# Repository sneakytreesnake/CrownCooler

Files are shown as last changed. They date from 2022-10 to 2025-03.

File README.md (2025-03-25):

# CrownCooler - Ring shaped CPAP cooling duct for Voron 3D printers
This mod is designed to adapt a fan mounted somewhere on the frame, through a CPAP tube and onto a "crown" shaped cooling duct. It has been designed for the Voron 2.4 and Voron Trident series of printers, mounting directly to the stealthburner X carriage.

 

This mod was developed to:
- be compatible with standard voron stealthburner carriage
- be compatible with all extruder combinations that are compatible with the stealthburner system, (CW1, CW2, Orbiter, LGX Lite, etc.)
- mount a Rapido HF/UHF hot end & Dragon SF/HF/UHF hot end 
- improve overall cooling performance by accomodating very large fans and intaking cool air from outside the heated enclosure
- provide uniform cooling from all directions
- be lightweight and easy to maintain
- work with klickyprobe & euclid probe.

The design of the crown duct creates a fluid vortex at the tip of the nozzle, resulting in high cooling performance. It was designed using commercial CFD software, and validated experimentally. There is a secondary air cooling route fed by the part cooling fan to prevent warping of the duct from hot end heat. 

**This mod is still a BETA. Expect issues - but let me know about them so I can fix them.**

## Dev Update (Mar 2025)
I've uploaded the Fusion 360 native CAD assembly.



I am currently testing the Dragon SF/HF version. Working well so far. 
My Rapido hotend is damaged so I can no longer test that one personally.

## Dev Update (Sept 2024)
I have added a trimmed down X carriage mount to fit the new duct. I've also added a adapter mount for the Euclid Probes. Let me know if there is interest for a Klicky mount and I will make one.

## Dev Update (August 2024)
I have created a Dragon (SF/HF) toolhead mount.  


Furthermore, I have created a new duct design. This combines the ideas I have created in the crown design, along with the tentacool duct. I'm still working on airflow optimisation but so far the performance is good.

The Dragon mount will be released in the coming days, and the duct will be released after some more testing.

## Dev Update (July 2024)
After a lot of experimenting with other cooling designs such as the [Tentacool](https://github.com/MirageC79/HextrudORT/tree/main/files/COOLING/TENTACOOL), I plan on merging the ideas produced from the V2.5 cooler, with the ideas from the Tentacool. I don't want to give a release date as it's a slow process, but a release is on the hoizon. 

Until then, I will build in support for other hot ends (dragon HF, Rapido HF, Rapido UHF for now. I am open to further requests). These will be release as soon as possible. The V2.5 duct and a modified Tentacool duct will be included in this release. I expect to release this by the end of July.

## V2.5 Update (February 2024)
The flow path has been updated in the latest version. It provides approximately **twice the cooling performance compared to the previous version!** In my testing, I was able to print 80degree angles at 30% fan rate (WS7040) with an enclosure temperature of 70C, 0.6mm nozzle size and 0.3mm layer height.

  

# Gallery

  

## CFD results:
You can clearly see a vortex being formed around the ring. This creates a cycle of air that rapidly carries heat from the printed part, allowing printong of steep overhangs.

 

# Part Cooling Fan Options

There are a number of part cooling fan options to choose from, depending on your intended use case.

### 4028 fan



A "medium" performance option is to use a 4028 fan on the end of the CPAP tube. This solution is best suited for ABS and similiar materials that do not require high amounts of part cooling. I do not recommend this option for printing PLA at high speeds.
A 4028 to CPAP tube adapter part is included in the STL files folder.

Recommended 4028 fans include:
- Sanyo 9GAX0412P3S001
- Delta FFB0412UHN-SM36

### 7040 blower fan



A "high" performance is to use a 7040 blower fan on the end of the CPAP tube. This solution is best suited for printing PLA & PETG & ABS at very high speeds.

A 7040 blower fan mount can be found [here.](https://www.printables.com/model/324265-ws7040-centrifugal-blower-fan-mount)

I recommend the WS7040 along with the controller board. I purchased mine from [Trianglelab here.](https://www.aliexpress.com/item/1005003822117604.html)

# BOM
- Coming soon...
  
# Installation instructions 
- This mod uses the standard stealthburner X carriage parts. T
- This mod should work with all types of extruder mounting parts, including CW2 (however, I have not yet tested it). I use the orbiter V2 extruder mount found [here](https://github.com/sneakytreesnake/StealthOrbiter).
- Print the cooling duct with no supports, file in STL folder. Use standard Voron print setting (0.6mm nozzle is acceptable)
- Only euclid and klicky probes are compatible at the moment. Use the offset klicky mount for HF hot ends, use the tall offset clock mount for UHF hot ends.

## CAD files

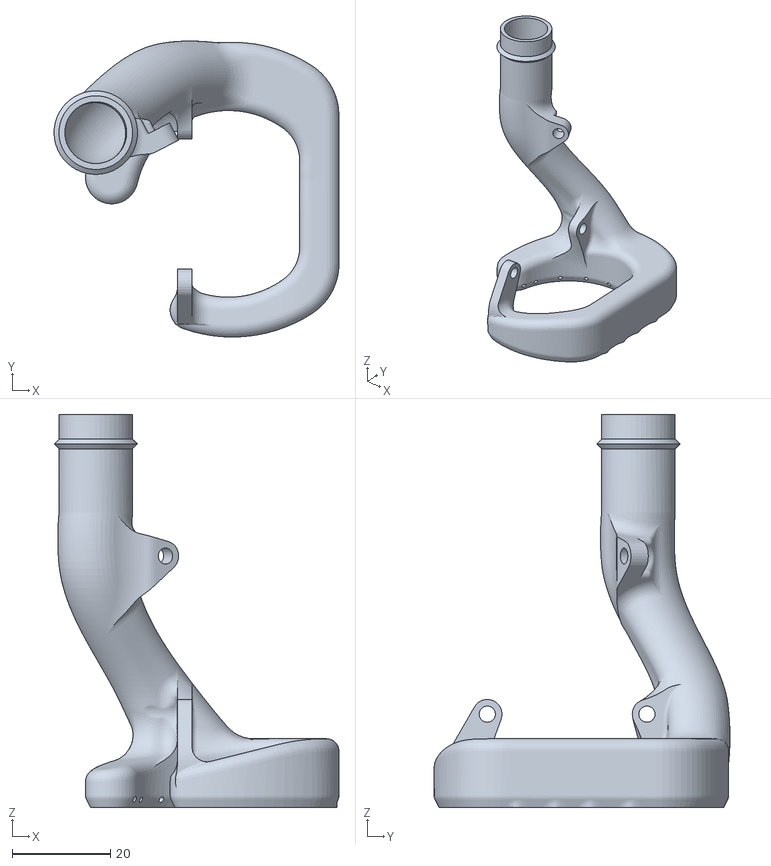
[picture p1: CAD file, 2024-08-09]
STL/Duct/MainDuct_BETA1.stl
58.0 x 60.3 x 80.0

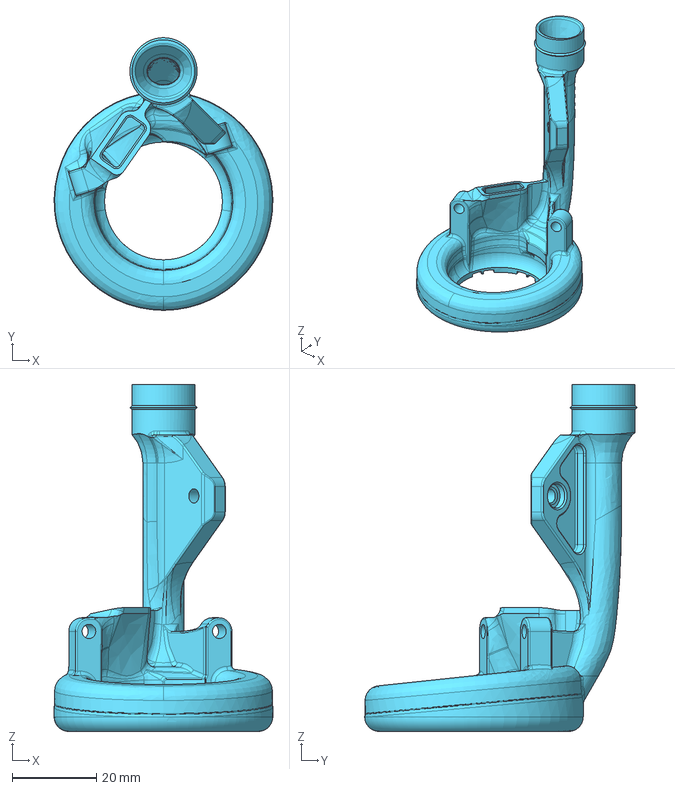
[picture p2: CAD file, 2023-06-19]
CAD/CrownCooler_Duct_RapidoUHF-15mmTube.step
52.0 x 64.8 x 82.5 mm

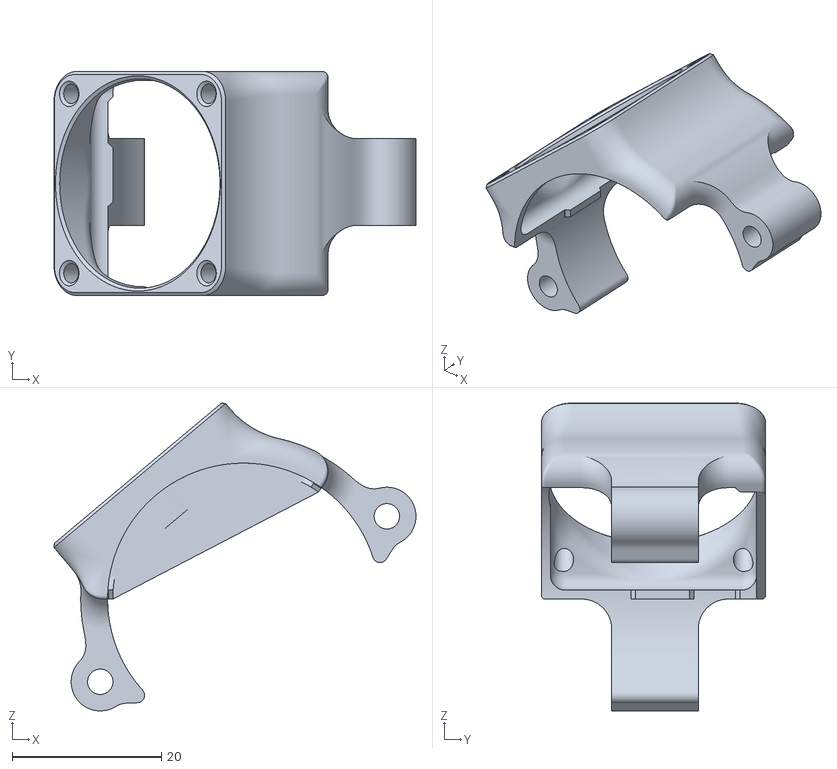
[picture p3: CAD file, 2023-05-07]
STL/ExtruderCooler/CrownCooler_ExtruderFanShroud.stl
48.5 x 30.0 x 41.2

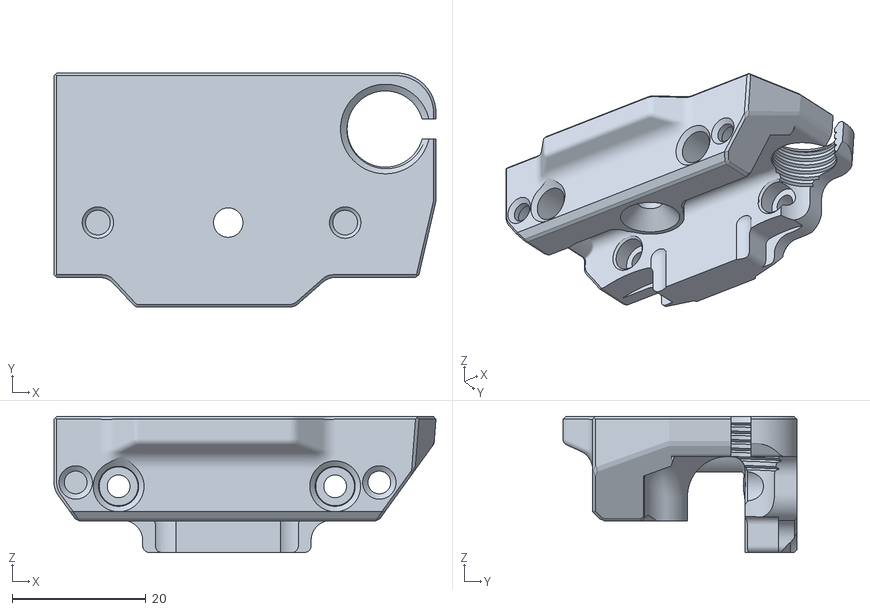
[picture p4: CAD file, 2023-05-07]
STL/ExtruderMount/CrownCooler_Orbitermount_Standard_PG7.stl
57.2 x 35.0 x 20.4

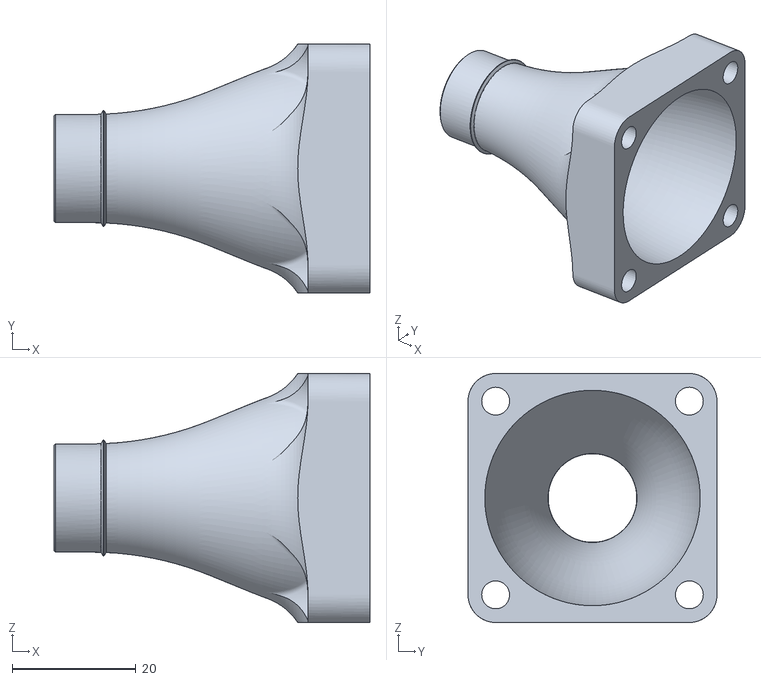
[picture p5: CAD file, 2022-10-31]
STL/FanMounts/4028 Fan/CrownCooler_4028FanCPAPAdapter.stl
51.0 x 40.2 x 40.2

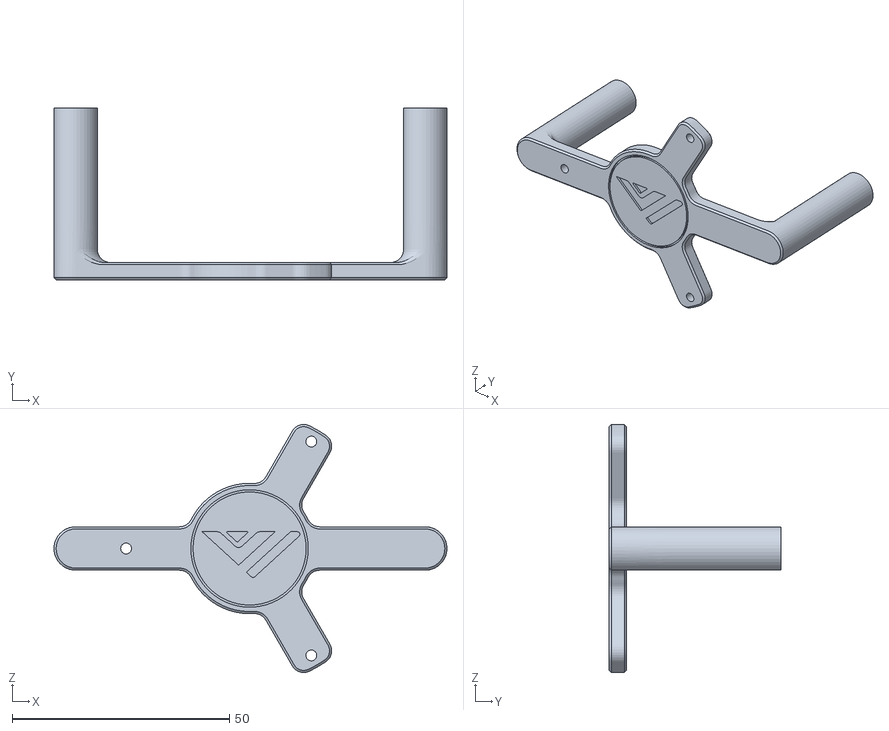
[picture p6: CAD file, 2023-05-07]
STL/FanMounts/WS7040 Fan/CPAPFanMount.stl
90.4 x 39.5 x 57.1

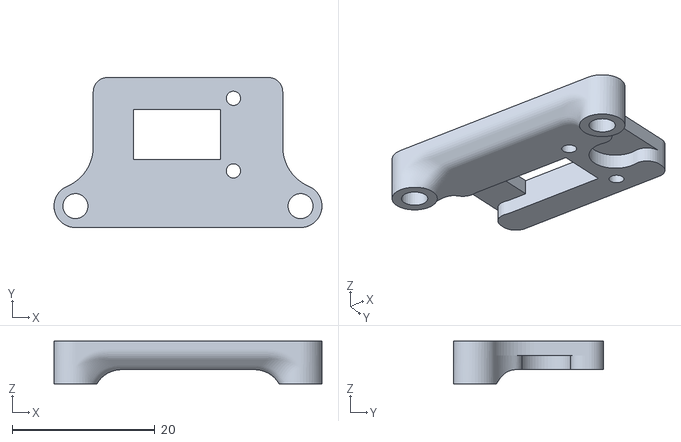
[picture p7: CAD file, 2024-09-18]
STL/ProbeMounts/EuclidProbeMountV2.stl
37.5 x 21.0 x 6.00

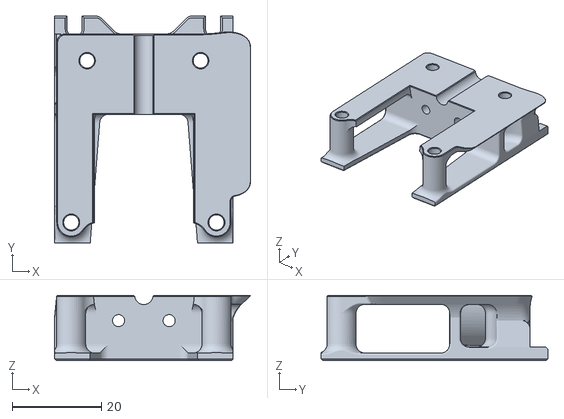
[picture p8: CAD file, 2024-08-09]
STL/Toolhead/CrownCooler_Toolhead_DragonHF_Rear.stl.stl
43.9 x 50.8 x 14.6

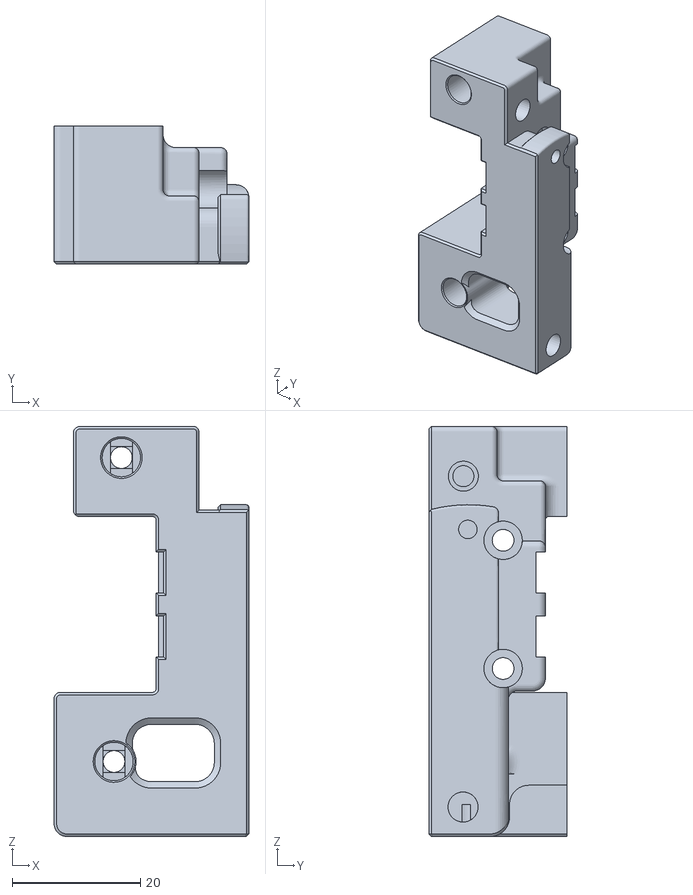
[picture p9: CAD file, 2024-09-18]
STL/Xcarriage/MGN12_X_Carriage_CW2_TRIMMED_left_V1.stl
30.4 x 21.6 x 64.0

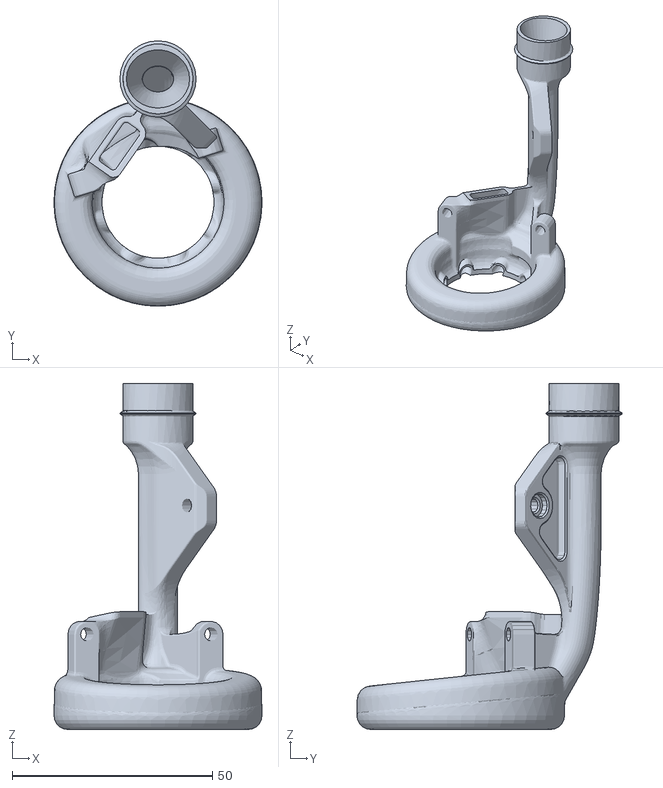
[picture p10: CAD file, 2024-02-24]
STL/Duct/CrownCooler_Duct_RapidoUHF_V2.5.stl
52.0 x 66.4 x 86.5

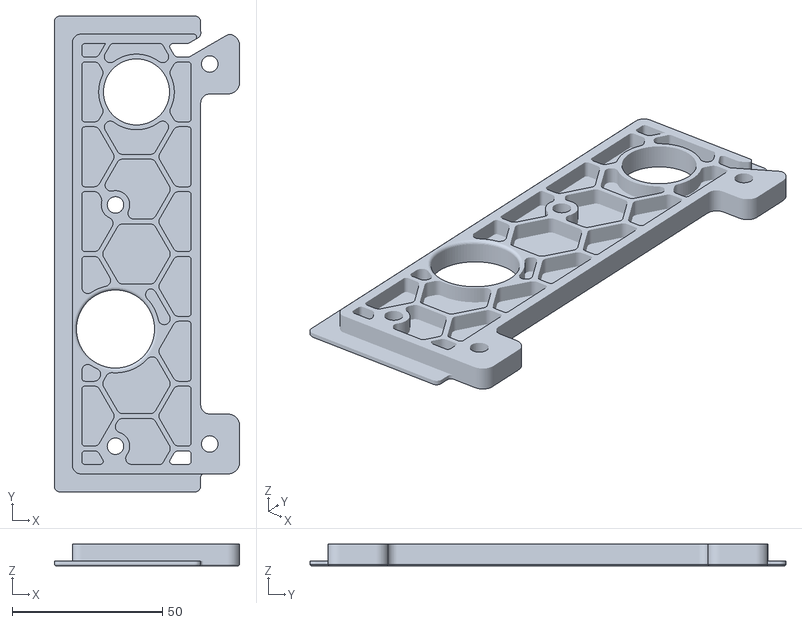
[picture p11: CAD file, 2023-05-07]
STL/FanMounts/WS7040 Fan/CrownCooler_ExhaustCover.stl
61.8 x 158.6 x 7.20

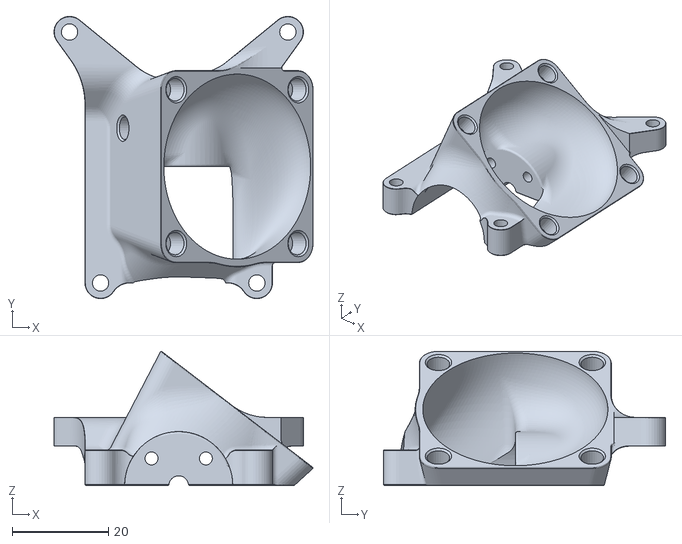
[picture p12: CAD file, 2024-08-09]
STL/Toolhead/CrownCooler_Toolhead_DragonHF_Front.stl.stl
53.9 x 58.7 x 27.9

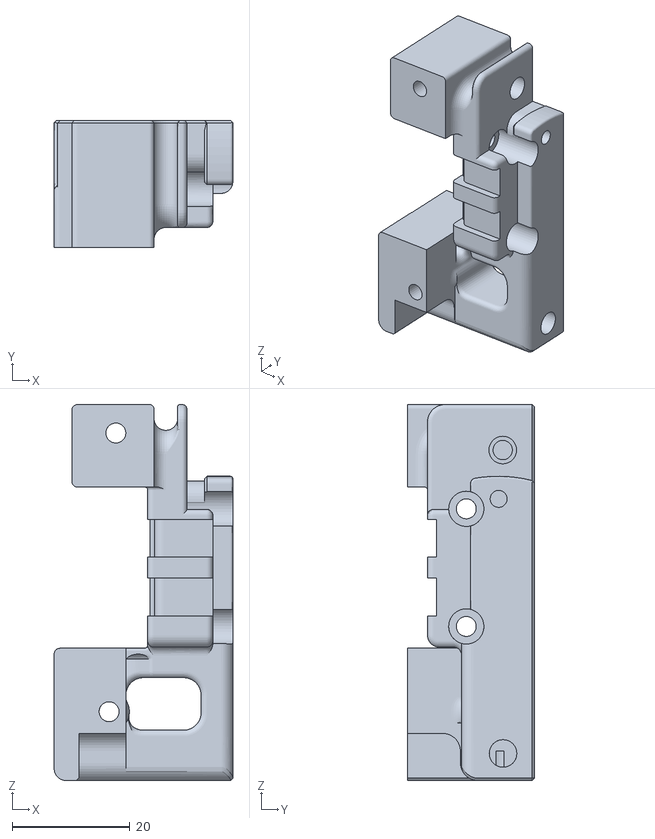
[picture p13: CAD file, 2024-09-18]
STL/Xcarriage/MGN12_X_Carriage_CW2_TRIMMED_right_V1.stl
30.4 x 21.6 x 64.0

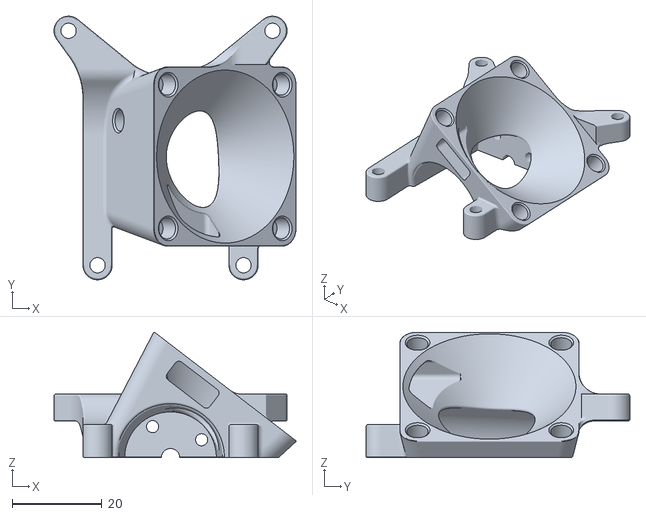
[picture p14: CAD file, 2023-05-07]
STL/Toolhead/CrownCooler_Toolhead_Rapido_Front.stl
53.9 x 58.7 x 27.9

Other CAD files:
STL/Duct/CrownCooler_Duct_RapidoUHF-15mmTube.stl
STL/FanMounts/WS7040 Fan/CrownCooler_ExhaustCover_PG7.stl
STL/FanMounts/WS7040 Fan/CrownCooler_ExhaustCover_PG7_Insert.stl
STL/Toolhead/CrownCooler_Toolhead_Rapido_Rear.stl
Legacy/STL/Duct/CrownCooler_Duct_RapidoUHF-15mmTube_V2.stl
Legacy/STL/Duct/CrownCooler_Duct_RapidoUHF_V2.stl
Legacy/STL/Duct/HaloDuctLongOverhangHF-DragonRevB.stl
Legacy/STL/Duct/HaloDuctLongOverhangHFRevB.stl
Legacy/STL/Duct/HaloDuctLongOverhangUHF-DragonRevB.stl
Legacy/STL/Duct/HaloDuctLongOverhangUHF-RapidoRevB.stl
Legacy/STL/Klickymount/KlickyOffsetRevA.stl
Legacy/STL/Klickymount/KlickyOffsetTallRevA.stl
Legacy/STL/Toolhead/PRINTHEAD_FRONT_DRAGONRevB.stl
Legacy/STL/Toolhead/PRINTHEAD_FRONT_RAPIDORevB.stl
Legacy/STL/Toolhead/PRINTHEAD_REAR_DRAGONRevA.stl
Legacy/STL/Toolhead/PRINTHEAD_REAR_RAPIDORevA.stl
STL/Duct/CrownCooler_Duct_RapidoUHF.stl
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

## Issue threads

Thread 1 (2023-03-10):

Unsure what fan to use

StackingDeezLayers, 2023-03-10:
I don't even know what fan to use. That should probably be something you specify. Thanks!

sneakytreesnake, 2023-03-10:
Did you mean the part cooling fan or the hotend fan?

The hotend cooling fan is a 2510 fan.

StackingDeezLayers, 2023-03-10:
> Did you mean the part cooling fan or the hotend fan?
>
> The hotend cooling fan is a 2510 fan.

I meant the part cooling fan. Thanks!

StackingDeezLayers, 2023-03-10:
Thank you, I appreciate that very much. I'll definitely look into doing this once my trident is done. It looks like an amazing part cooling solution

Also, I see you still are using the normal 2020 extrusion on the X-axis. Maybe consider carbon fiber? Here is great video explaining the whole light X-axis thing: https://youtu.be/Yzr6elGFR44

Closed 2023-03-10.

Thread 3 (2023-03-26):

Collision with front doors

madnezzm, 2023-03-26:
Voron 2.4 300mm. Rapido hotend
The air duct is in contact with the front doors. Fan goes further.
Need a more compact size by 12-15mm on the Y axis, not including the fan
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

sneakytreesnake, 2023-03-27:
You are correct in that the duct will hit the front panel when moving the toolhead to Y=0. I do intend to fix this in the near future once the more pressing issues have been resolved.

Is there a particular reason that you are mounting the fan directly on the toolhead? One of the main benefits of the CPAP designs is to take the weight of the high powered fans off the toolhead. It was intended that the fan, in your case the 4028 fan, is mounted either to the gantry or outside the enclosure.

sneakytreesnake, 2023-03-28:
I am still actively developing (including moving the duct in so it doesn't hit the doors) so I won't release the CAD just yet.

Once the designs are a bit more finalised, I will release the CAD.

Closed 2024-02-04.

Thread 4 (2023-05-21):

V2 cooler w/Orbiter Filament Sensor

ndng28, 2023-05-21:
Any plans to add extruder motor cooling compatibility with Orbiter v2 Filament sensor?

sneakytreesnake, 2023-05-30:
Have you considered using the [Turbiter](https://www.orbiterprojects.com/turbiter/)? It is made by the same developer as the orbiter & orbiter sensor.

ndng28, 2023-05-31:
Thanks for the link. I was not aware of the turbiter project but it won't fit my use case since I am using a EBB36 board.

sneakytreesnake, 2023-06-03:
To answer the original question, I don't plan on making another extruder cooler that is compatible with canbus boards and the orbiter sensor at the same time.

ndng28, 2023-06-03:
No worries. Thanks

On Sat, Jun 3, 2023 at 4:40 PM sneakytreesnake ***@***.***>
wrote:

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
--
Thank you,
Navish Dadighat

Closed 2023-06-03.

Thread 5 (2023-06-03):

V2 When?

BlackShadeOSS, 2023-06-03:
I was wondering when the v2 will come out, because I realy like the design but v2 looks like its more compact.

BlackShadeOSS, 2023-06-03:
I also would be happy to test it.

sneakytreesnake, 2023-06-03:
Hi, the V2 is already out, just check the STL files.

FYI, the V2 only supports the rapido UHF hotend for now. I'll add some more in the future.

BlackShadeOSS, 2023-06-04:
oh I need dragon hf version

sneakytreesnake, 2023-06-05:
Understand, Ill make a dragon HF version next.

BlackShadeOSS, 2023-06-05:
thanks for your awesome work

BlackShadeOSS, 2023-07-25:
Any update on dragon hf version ?

BlackShadeOSS, 2023-10-08:
@sneakytreesnake any updates?

sneakytreesnake, 2024-09-18:
A dragon HF version has been added

Closed 2024-09-18.

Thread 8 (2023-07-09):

Update BOM?

kayboy-bebop, 2023-07-09:
The readme BOM still specifies parts for the V1. Looking at the STLs for V2 the fans seem to be 40x40 for the toolhead and 30x30 for the extruder.

Any possibility of a BOM update?

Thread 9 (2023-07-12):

WS7040 Wiring and configuration

Maceon12, 2023-07-12:
I am attempting to set up a ws7040 on my voron trident using a v1.1 octopus board and have found that the fan is turning on at max speed as soon as the printer turns on. This appears to be because the octopus drives the pwm on the ground pin, instead of the 5v pin. Because of this the fan has to be driven off the raspberry pi which is not intuitive for most users. Can a guide on the wiring be added to the instructions. Alternatively, the yotube channel Vez3D has an excellent tutorial on the cpap remote cooling setup (https://youtu.be/E3kBau82SwU) so a link to his video would also be useful, either in place of or alongside wiring and config instructions.

Ekodas, 2023-11-20:
I haven't wired mine up just yet, but I believe the work around for this is to actually use one of the Octopus boards endstop pins instead of a fan header pin.

realJosef, 2023-12-28:
just finished my Installation yesterday.

this link will show you how to setup the pwm fan. i used 24V+ from the PSU and a heater - for the GND wire. PWM is on a FAN-
https://os.ratrig.com/docs/guides/4028/

sneakytreesnake, 2024-05-28:
answered by @realJosef

Closed 2024-05-28.

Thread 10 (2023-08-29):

New fan option suggest : dual rotor 4056

ChipCE, 2023-08-29:
I'm using 4056 fan on my printers and it gives quite good result. I think the output power will be in the middle between 4028 and CPAP.
In my setup, I use quite small tube so i need an extra adapter with 5015 fan to reduce the back flow. I think it will work as-it in your design.
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

https://www.aliexpress.com/item/1005003803489167.html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

sneakytreesnake, 2024-05-28:
Hi, thanks for the suggestion.

The focus of this mod is closer to adapting a CPAP tube to a voron style carriage.
While I have included a few different options to attaching to fans (WS7040, 4028), I largely consider further fan support up to the end user (i.e. not this mod).

Closed 2024-05-28.

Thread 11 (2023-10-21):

Can it be made compatible with other extruders?

Mapte146, 2023-10-21:
Hello, I understand it's made specifically for a Voron printer but I really like the design of the crown style cooling duct. I am
wondering if it can be used for my Sprite extruder for my CR 10 smart pro. Is there a way you can modify the design to fit sprite extruder? or if you can upload stp file of the crown portion of your design I can modify it too so it can be used for my sprite extruder. Thank you.

sneakytreesnake, 2024-02-24:
Hi, thanks for the suggestion.

It looks like the sprite extruder is significantly different than the Voron Stealthburner style, so I am not sure it will work without a complete re-design.

For now, I want to keep this design focused on the Voron range of extruder/carriage systems.

Closed 2024-02-24.

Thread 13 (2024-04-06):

Is this toolhead compatible with the BTT Ebb Sb2209?

cray12399, 2024-04-06:
Hi, first of all, this toolhead is absolutely impressive and thank you for the hard work in designing it.

I really want to add it to my build, but I am using the BTT Ebb sb2209. Is this toolhead compatible with that board? Or if not, are there plans to make it compatible in the future?

cray12399, 2024-04-06:
Also, is it compatible with Bowden via the m4?

realJosef, 2024-04-06:
Hi,
i've nothing to do with this project but use the printhead and love it since.
i think i can give you a clear no for both questions.

The sb2209 is made for Stealthburner and nothing else.

realJosef, 2024-04-06:
Yes the M4 is based on the CW2 but only the internal design its not meant to be mounted to the toolhead.
I dont think that the work will give you any benefits.

cray12399, 2024-04-06:
@realJosef Yes, the Mobius has an external extruder mechanism that is mounted away from the toolhead, but there is also a clockwork-style body that mounts to the toolhead and routea the filament to the hotend. It uses the same mounting mechanism as the clockwork so I don't see a reason it shouldn't work. Here's a link to it: https://github.com/VoronDesign/Voron-Stealthburner/tree/main/STLs/Clockwork2/Bowden

realJosef, 2024-04-06:
Sorry i think i miss understood you. i thought you wanted the m4 ON your toolhead.
This could work for sure. you only need to adapt the frontcover for the can board then.

sneakytreesnake, 2024-04-07:
@realJosef answered correctly, this mod doesn't directly supported Bowden inputs or have any mounting hardware for the BTT EBB SB2209.

In saying that:
1) this mod maintains combability with the stealthburner system. It uses the standard stealthburner x carriage, and all the mounting hardware is the same. So if you wanted, you could use a stealthburner bowden mod, like [here ](https://www.printables.com/model/139183-ender-3-v2-voron-stealthburner-conversion/files)(though I haven't tested this)

2) There is enough space around the toolhead to make a SB2209 mount... but it will be kinda jank. I use a EBB36 and this mounts well within the whole assembly.

Closed 2024-04-07.

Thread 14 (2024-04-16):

Dragon HF not fitting

Burtila, 2024-04-16:
Hi, try to fit a dragon HF hotend, but is not is not possible.
Do you have some extra component for dragon hf?
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

sneakytreesnake, 2024-04-17:
Noted, it doesn't fit. Will need to update.

I will have to release a new duct to be compatible with dragon HF/Rapido HF for it to be compatible. Will close this issue once I've made that update.

zerosnugget, 2024-05-26:
Are you already working on that update? I also use a Dragon HF and would like to use the newer version of this mod.

Burtila, 2024-06-21:
Hi, i don`t what to be pushy, but the update will be available soon?

sneakytreesnake, 2024-06-22:
I'm aiming to have a dragon HF version ready sometime in July.
Fitting the duct in with a much shorted hotend is proving to be somewhat of a challenge though.

Burtila, 2024-09-01:
Any update?

sneakytreesnake, 2024-09-08:
I have uploaded dragon toolhead STLs [here ](https://github.com/sneakytreesnake/CrownCooler/tree/main/STL/Toolhead).

However, if you are using the standard X carriage you will have fitment problems with the duct (the metal ones are fine). Ill update this soon.

sneakytreesnake, 2024-09-18:
Added X carriage

Closed 2024-09-18.

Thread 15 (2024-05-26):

Financially supporting your projects

zerosnugget, 2024-05-26:
This is more of a general question, but I'm mostly interested in the crowncooler mod so that's why I'm opening the issue here. I would like to ask, if there is any way to support you financially to most importantly help you working on your projects and maybe also speed things up a little. I didn't see any option to be a GitHub Sponsor so that's why I'm asking.

Thank you for your effort so far!

sneakytreesnake, 2024-05-28:
Hello,

I'm running behind on developing most of these projects lately due to having to pick up an extra job... so this may not be a bad idea.

I haven't heard about Github Sponsors before, so I've set up an account now. I am sure it will appear on my account soon.

In terms of actually making some progress on this project, are you able to contact me on discord to describe your setup (hotend, probes, etc)?

zerosnugget, 2024-06-17:
Hey,
thx for the quick response and sorry for taking so long to answer. I don't know if you've got any response from Github yet but there is still no sponsor button on your profile. Maybe this really would help you if you've financial issues. I hope it gets unlocked soon and a couple of people consider supporting you! I can, but I still want to state here that I'm using the Dragon HF in combination with the Orbiter V2 extruder and a Beacon.
For the X carriage to support the Beacon sensor I've been using this 180° degree version: [https://www.teamfdm.com/files/file/686-beacon-cw2-stealthburner-alternative-mounts/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](https://www.teamfdm.com/files/file/686-beacon-cw2-stealthburner-alternative-mounts/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)

I've recently printed the "legacy" Parts for my build because the Dragon Hotend is still missing in the new version. So far it's working great except the 2510 Fan blowing against the Hotend Cooler worries me a bit (there aren't many options as far as I could find especially for 24v and it seems pretty weak)

sneakytreesnake, 2024-06-19:
No worries.

I'm working on a new release, aiming for July. I'll do my best to include support for the beacon sensors and dragon HF hotends.

I'll see if I can get the sponsor system to work, but I want to make it clear that I have no expectations for support :-)

zerosnugget, 2024-06-19:
I'm looking forward to that! Like I said the 180 Degree Version works perfectly (it justs offsets the mount further to the back. I can attach a picture later to this thread.

Yeah of course that's totally reasonable!

Korolen, 2024-07-04:
@sneakytreesnake I looked at both the repo page and your user page, and I still don't see the option to sponsor? I'd love to chip in as well to help the project along and show appreciation.

sneakytreesnake, 2024-07-04:
Hi @Korolen . Firstly, thank you for your support!

Unfortunately, I am still waiting for Github themselves to review my profile. I'm submitting a support ticket to see if that makes some progress...

In any case, I'll update this thread once it has gone through :-)

sneakytreesnake, 2024-07-05:
Hi all,

Support has come back and approved my github sponsors account :-)

Closed 2024-07-05.

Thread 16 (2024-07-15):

Tap Support

S1L3NTANG3L, 2024-07-15:
Not an issue but a question XD, Want to run this with tap and was wondering if you have though of an version that'll work?

sneakytreesnake, 2024-07-21:
Hello,

I haven't checked if it's compatible with TAP yet.

Could you give me an idea of your setup so I can check? What hotend, probe, etc are you using?

S1L3NTANG3L, 2024-07-22:
I'm busy building a Trident but I had a bit of a think and the tap is the better option in terms of rigidity, great design btw!

Closed 2024-07-22.

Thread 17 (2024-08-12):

Endoscope nozzle cam mount?

Nathan22211, 2024-08-12:
thus far it seems there isn't any way for a nozzle cam on this toolhead. I only suggested an endoscope because they're cheap for 720p ones, especially off of Temu, and using a hardwire one could double for the piano wire in an umbilical, but that may need a custom gland.

sneakytreesnake, 2024-09-08:
I am not currently planning for this. I will upload the native CAD files when I have finished a few updates if you want to make the changes yourself.

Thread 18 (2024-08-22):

New beta duct may interfere with carriage

woodencliff, 2024-08-22:
[crown mount on xol carriage.zip](https://github.com/user-attachments/files/16707495/crown.mount.on.xol.carriage.zip)
Looking foward to your design! I'm planning to migrate from xol toolhead to CrownCooler. I imported the new beta duct into cad and tried to assemble, found that the rear part is colliding with the bottom of carriage. I'm using xol carriage(https://github.com/Armchair-Heavy-Industries/Xol-Toolhead/blob/main/STL/Xol-Carriage/Xol-Carriage_MGN12H.stl) ,and the stock cw2 carriage has a even larger chin, which may cause a even bigger problem.

sneakytreesnake, 2024-09-08:
Updating the carriage will be in the next update.

Alternatively, the "cartographer metal bracket" x carriages are already compatible.

sneakytreesnake, 2024-09-18:
I've added a trimmed down X carriage.

Closed 2024-09-18.

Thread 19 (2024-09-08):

Current Rapido duct interferes with TAP

Nathan22211, 2024-09-08:
at least it interferes with the vatali tap, but it seems any tap it interferes with

sneakytreesnake, 2024-09-08:
You are correct. I will add compatibility with TAP in the next update.

Nathan22211, 2024-09-09:
LMK when you do I've been printing out klicky parts on my 2.4. which I haven't dialed in yet

Nathan22211, 2024-09-11:
I quickly cut and capped off the conflicting area in tinkercad so hopefully, that can be a temp fix

Nathan22211, 2024-09-13:
for those who find this issue, I remixed the duct in Tinkercad to cut the back half off. I also made an endoscope version
https://www.printables.com/model/1006095-tiara-cooler-tap-compatible-crown-cooler

Nihont0, 2024-10-18:
Hi, any updates on TAP compability? I really want to try Crowncooler on my Voron 2.4 but I also have a Chaoticlabs TAP installed...

@Nathan22211 How is the cooling with you "Tiara Cooler" Mod?

Nihont0, 2024-10-18:
Okay thanks, I will try it out then!

Nihont0, 2024-10-24:
@Nathan22211 unfortunately the duct interferes with the Extruder, I am using a Galileo 2 Stand alone. Which extruder did you use?

[image](https://github.com/user-attachments/assets/0efbd0d7-280d-47c9-ba4c-6d05c34946bb)

Nathan22211, 2024-10-24:
Orbiter 2.0 with the included mount.

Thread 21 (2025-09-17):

possibility to add a regular fan set up to it rather that a cpap

justYZN, 2025-09-17:
i love the simple light weight that this tool head has but setting up cpap is pain to me i print only in abs and pc so i don't want that much of a cooling i tried the suggested fan for abs use but the quality dropped than what i used to have with the sb if there is a way to reuse the Part cooling fan that comes with the SB and attached it to the toolhead

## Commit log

2022-10-07 added STLs
    [HaloDuctLongOverhang v9.3mf, KlickymountV13.3mf, RapidoLongFront.3mf]
2022-10-31 Added Rapido HF variant
    + organised files
    [4028FanCPAPDuct v2.stl, HaloDuctRapidoHF v4.stl, HaloDuctRapidoUHF v9.3mf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]
2023-02-03 added dragon files
    yet to test dragon files. Rapido HF has been tested to work.
    [4028FanCPAPDuct.stl, CrownDuctDragonHF.stl, CrownDuctDragonUHF.stl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]
2023-02-14 few errors on UHF dragon design, updated. Added UHF rapido
    [CrownDuctRapidoUHF.stl, FrontBodyDragon.stl, FrontBodyRapido.stl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]
2023-05-07 Crowncooler V2 (Rapido UHF)
    - Remodelled toolhead
    - Added extruder stepper cooler duct
    - part cooling fan changed to 4010 fan
    - directed some hotend cooling fan airflow to cool duct to prevent heatcreep
    - added crowncooler-specific extruder mount
    - added klickymount
    [4028FanCPAPDuct.stl, CrownCooler_4028FanCPAPAdapter.stl, CrownCooler_Duct_RapidoUHF.stl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]
2023-05-07 added non-PG7 CPAP fan grill mount
    [CPAPFanMount.stl, CrownCooler_ExhaustCover.stl]
2023-06-19 added rapido UHF duct to fit 15mm CPAP tube
    [CrownCooler_Duct_RapidoUHF-15mmTube.step, CrownCooler_Duct_RapidoUHF-15mmTube.stl]
2023-06-19 added toolhead CAD assembly
2024-02-24 revised rapidoUHF duct to V2.5
    moved V2 to legacy folder
    [CrownCooler_Duct_RapidoUHF-15mmTube_V2.stl, CrownCooler_Duct_RapidoUHF_V2.5.stl, CrownCooler_Duct_RapidoUHF_V2.stl]
2024-08-09 added new duct design, BETA 1
    [MainDuct_BETA1.stl]
2024-08-09 Added Dragon HF support
    [CrownCooler_Toolhead_DragonHF_Front.stl.stl, CrownCooler_Toolhead_DragonHF_Rear.stl.stl]
2024-09-18 added trimmed X carriage
    [MGN12_X_Carriage_CW2_TRIMMED_left_V1.stl, MGN12_X_Carriage_CW2_TRIMMED_right_V1.stl]
2024-09-18 removed obsolete klicky mounts
    [CrownCooler_KlickyProbe_RapidoUHF.stl, CrownCooler_Klicky_DragonUHF.stl, CrownCooler_Klicky_HF.stl]
2024-09-18 added euclid probe mount
    [EuclidProbeMountV2.stl]
2025-03-25 added fusion CAD files
    for CrownCooler V2.5 assemblies
